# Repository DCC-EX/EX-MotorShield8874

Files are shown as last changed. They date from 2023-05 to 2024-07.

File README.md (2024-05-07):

# EX-Motorshield8874

## Overview
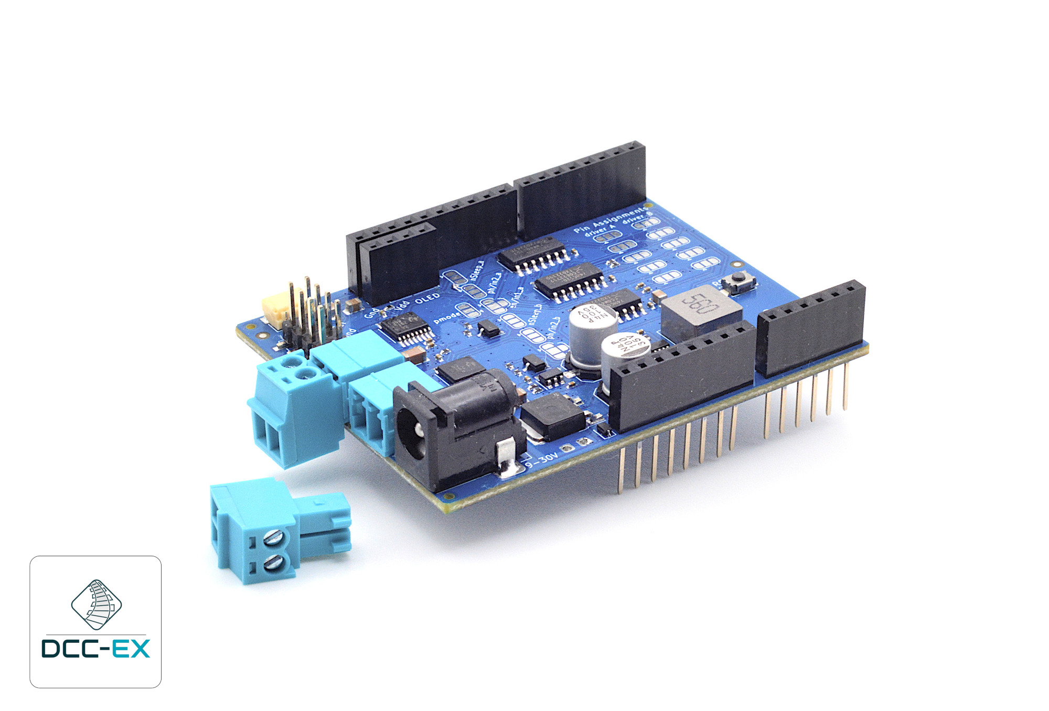
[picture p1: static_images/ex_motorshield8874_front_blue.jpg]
DCC-EX EX-MotorShield8874


The EX-Motorshield8874 is a pin compatible with the original [Arduino Motor Shield Rev3](https://store.arduino.cc/products/arduino-motor-shield-rev3) but provides significantly improved electrical performance for driving higher loads, with lower power dissipation, and improved usability.

The EX-Motorshield8874 is based on two DRV8874 H-bridge motor drivers with integrated current sensing from Texas Instruments (TI). It is used to drive inductive loads like relays, solenoids, DC and stepping motors.

Powering of Arduino motherboard is possible due to the onboard DC/DC buck converter, supporting a wide input supply range from 9 to 30V. The reverse polarity protection prevents damage to the circuit and its components in case the power supply is accidentally connected with reversed polarity.

This Shield features a green status LED which provides a visual indication of the power supply status.

### Compatibility with [Arduino Motor Shield Rev3](https://store.arduino.cc/products/arduino-motor-shield-rev3)

The EX-MotorShield8874 is pin compatible with the original Arduino Motor Shield but provides significantly improved electrical performance for driving higher loads. Input voltage range is 9-30VDC and the maximum peak output is 5A per channel, in contrast to 5-12VDC and 2A peak for the original Arduino Motor Shield.

There is also almost no voltage drop incurred from the input voltage due to the MOSFET based design, unlike the bipolar L298 used in the Arduino Motor Shield. For DCC and DC PWM model railway use, a range of 10-24VDC is recommended depending on scale.

### Motor Driver Configuration for DCC-EX EX-CommandStation

The EX-MotorShield8874 will work with the `STANDARD_MOTOR_SHIELD` definitions in `MotorDrivers.h`, but that is not ideal for several reasons. It will both unnecessarily limit current output, ignore the fault pin, and not read current correctly.

The following motor definitions are required, and appear in later versions of EX-CommandStation, with the tag `EX8874_SHIELD`, which will differ according to whether the Command Station is an UNO or Mega with 5V 10-bit ADC, or a 3.3V capable system with 12-bit ADC:

```c++
// EX 8874 based shield connected to a 5V system (like Arduino UNO/Mega) and 10bit (1024) ADC
#define EX8874_SHIELD F("EX8874"), \
 new MotorDriver( 3, 12, UNUSED_PIN, 9, A0, 5.08, 5000, A4), \
 new MotorDriver(11, 13, UNUSED_PIN, 8, A1, 5.08, 5000, A5)

// EX 8874 based shield connected to a 3V3 system with 12-bit (4096) ADC
#define EX8874_SHIELD F("EX8874"), \
 new MotorDriver( 3, 12, UNUSED_PIN, 9, A0, 1.27, 5000, A4), \
 new MotorDriver(11, 13, UNUSED_PIN, 8, A1, 1.27, 5000, A5)
```

## Control Pin Assignments

### Default Pin Assignment for DCC-EX/Arduino motor control

The EX-MotorShield8874 has the following default pin assignment for control pins on the Arduino header, and is used for full Arduino Motor Shield R3 compatibility when used for DCC-EX EX-CommandStation.

| Function | Channel A Pin | Channel B Pin |
|---|---|---|
| PWM       | D3  | D11 |
| Direction | D12 | D13 |
| Brake     | D9  | D8 |
| Current sensing | A0 | A1 |
| Fault_N   | A4  | A5 |

Default pin assignment is used for DCC-EX command stations, and has the DRV8874 mode select pin `PMODE` = high.

### Alternative Pin Assignment for DCC-EX/Arduino motor control 

All motor control signals can be connected to two different Adruino header pins. Selecting between the default pin out and the alternative pin out is done via solder jumpers on the PCB which must be first cut to disable the default position, then solder applied to select the alternate position.

| Function | Channel A Pin | Channel B Pin |
|---|---|---|
| PWM       | D2  | D5 |
| Direction | D10 | D4 |
| Brake     | D7  | D6 |
| Current sensing | A2 | A3 |
| Fault_N   | D0  | D1 |

NB: For DCC-EX control, these are not ideal pin assignments and are intended for future support of stacking of two shields. Further documentation updates will be available once testing of this mode is complete.

### Fault indicator

The H-Bridges are protected against supply undervoltage, charge pump undervoltage, output overcurrent and device overtemperature. Fault conditions are indicated on the pin `nFAULT` of the H-Bridge driver. The open drain output of the fault indicator is pulled low during a fault condition and pulled to high with the on board pull-up resistor. There is one fault indicator per channel.

**NOTE for UNO users:** the `nFAULT` pins are routed to the same pins used for I2C on the ATMEGA329P used on the Arduino UNO R3, namely A4 and A5. As such, if you are to use an EX-MotorShield8874 on an Arduino UNO, please cut the default track on the relevant jumpers to disable them. If you want to use the `nFault` pins you will need to manually jumper them to any available alternate digital input pins, then configure the Motor Driver entry in EX-CommandStation to suit the pins used.

### Alternative pin assignment for other motor control applications

The alternative pin assignment for motor control (PH/EN mode) allows to control the motor in a speed and direction type interface. This mode is selected via Jumper J101 (DRV8874 mode select pin `PMODE` = low) and is NOT required for use with DCC-EX. It is documented for completeness.

| Function | Channel A Pin | Channel B Pin |
|---|---|---|
| PH       | D3  | D11 |
| EN | D12 | D13 |
| Brake     | D9  | D8 |
| Current sensing | A0 | A1 |
| Fault_N   | A4  | A5 |

## Electrical Parameters

The DCC-EX Motor Shield provides the following electrical parameters.

| Parameter | Value |
|---|---|
| Operating voltage range | 9-30VDC, polarity protected|
| Maximum H-bridge current  | 5A peak per channel |
| Arduino supply voltage output (VIN) | 7.2V@2A max |
| IO voltage              | 3.3 and 5V, using IOREF by default |
| I2C connectivity        | Dupont, 2.54mm dual row pin, and STEMMA QT/Qwiic Headers |
| Current sensing         | Yes, adjusts range to IOREF voltage |
| Control modes possible | PWM, by default, PH/EN via jumper |

## Current Sensing

Current sensing is independently available for each channel. The Arduino IOREF supply voltage is sensed automatically, and adjusts the gain factor for the current sensing to take advantage of the full ADC input voltage range for 5V or 3.3V microcontrollers. The sense factors are calculated as follows for DCC-EX motor driver definitions:

| IOREF Voltage: | 5V | 3V3 |
|---|----|-----|
| 10-bit ADC, 1024 count | 5.08 | 4.94 |
| 12-bit ADC, 4096 count | 1.27 | 1.24 |

These values have been incorporated into EX-CommandStation Motor Driver definitions, so selecting `EX8874_SHIELD` as the `MOTOR_SHIELD_TYPE` in config.h will configure it correctly.

## Track LEDs

LEDs are provided for each channel, indicating the corresponding H-Bridge is supplying power to output connectors.

## Header Pin Assignments

The following pin assignments have been used for the various connectors.

### I2C Headers

Three I2C expansion headers (Dupont, dual-row 8-pin, and STEMMA QT/Qwiic) allow connecting either an OLED display or other additional I2C based devices.

#### Arduino Header

On the Arduino header, the default upper right I2C pins are used for I2C:

| Function | UNO R3 Pin | Mega Pin |
|---|---|---|
| SCL | D18/A5 | D21 |
| SDA | D19/A4 | D20 |

#### DIP Header

The dual-row 8-pin header has the following pin assignments:

| Function | Odd Pin | Even Pin |
|---|---|---|
| IOREF | 1 | 2 |
| SDA | 3 | 4 |
| GND | 5 | 6 |
| SCL | 7 | 8 |

#### OLED Header

The single-row 4-pin OLED header has the following pin assignments, which are standard for many I2C capable OLED displays:

| Function | Pin |
|---|---|
| GND | 1 |
| IOREF | 2 |
| SCL | 3 |
| SDA | 4 |

#### STEMMA QT/Qwiic Connector

STEMMA QT/Qwiic connector pin assignments are per the standard, but included for completeness:

| Function | Pin | Colour Code |
|---|---|---|
| GND | 1 | Black |
| 3v3 | 2 | Red |
| SDA | 3 | Blue |
| SCL | 4 | Yellow |

**NOTE** STEMMA QT power is tied to 3v3 as that is required for the standard. When using the EX-MotorShield8874 with 5V motherboards such as UNO and Mega, any I2C peripherals connected to the STEMMA QT connector **must** be 5V-tolerant only!

Pull-up resistors for the I2C communication are not populated by default. If required, pull-up resistors (R101, R102) can be populated on the board, though this is typically not necessary.

## Reset button

A reset button is provided to reset the Arduino board.

## PCB Jumpers

Various PCB jumpers are provided to alter functionality of the board to suit user needs. These include jumpers to alter pin assignments for driving the motor shield, to disable the onboard 7.2V regulator or disconnect it from the VIN, and jumpers to override the IOREF pin for ADC range selection.

### Aternate Pin Assignment PCB Jumpers

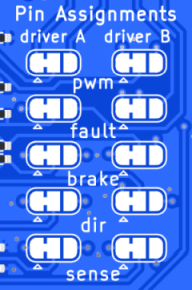
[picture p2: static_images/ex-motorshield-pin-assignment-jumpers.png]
Alternate_Pin_Assignments


There are 5 sets of PCB jumpers for each motor driver IC, some or all of which can be used to reassign Arduino pins to the various logic functions. The table below lists them in order as they appear on the PCB:

| Function | Driver A Default | Driver A Alternate| Driver B Default | Driver B Alternate |
|---|---|---|---|---|
| PWM       | D3  | D2 | D11 | D5 |
| Fault | A4  | D0 | A5 | D1 |
| Brake | D9  | D7 | D8 | D6 |
| Direction | D12 | D10 | D13 | D4 |
| Current sense | A0 | A2 | A1 | A3 |

### Power Configuration PCB Jumpers

There are 4 sets of PCB jumpers to change the way power is handled on the board. One on the top of the board, and 3 on the bottom, shown here:

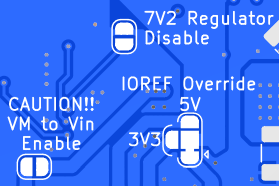
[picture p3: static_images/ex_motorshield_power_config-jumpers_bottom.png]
Bottom_Power_Config_Jumpers
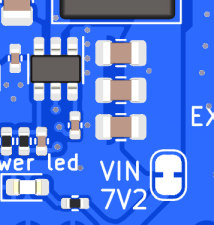
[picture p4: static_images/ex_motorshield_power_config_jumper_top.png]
Top_Power_Config_Jumper
 

| Jumper | Function |
|---|---|
| Regulator Disable (Regulator Enable on Rev A boards) | Defaults to *ENABLED*. Rev B boards, *solder* between pads to DISABLE onboard 7.2V regulator. Rev A boards *cut* between pads to DISABLE |
| IOREF Override | Defaults to IOREF used as power source, cut and then solder to either 5V or 3V3 to power logic and current sense |
| VM to Vin Enable (unlabelled on Rev A boards) | Defaults to NOT connected. CAUTION: soldering these pads CONNECTS motor power to VIN and should not be needed |
| VIN | Defaults to ON, cut to stop providing regulated 7.2V power to VIN to power the Arduino |

## Manufacturing Notes

### Bill of Materials (BOM)

The bill of materials spreadsheet above is optimised for manufacture at JLCPCB (https://jlcpcb.com/) at present, and will allow assembly of all components except the DC barrel jack, motor output connectors and Arduino shield stackable headers.

### PCB Material Specifications

For best performance, 1oz copper for both outer and inner layers of this 4-layer PCB are safest. Of course 2oz copper can be specified, but this is not deemed necessary from testing so far and cost may be prohibitive. Also, using FR-4 TG155 will give additional safety margin. The design can be made lead-free, provided all components are also lead-free types. JLCPCB currently does not have lead-free connectors for DCC track or DC input power, so those components are not in the default Bill of Materials (BOM).

## Stacking Multiple Shields

It is possibile to stack two EX-MotorShield8874s, and even stack an EX-MotorShield and a Arduino Motor Shield.

Produktfoto_3_4

There are two different proposed operating modes possible:

1. **Independent district mode:** The DCC-EX Motor Shields are controlled independently using different control signals. This allows a total 4 independent H-Bridges to be driven completely independently for separate DCC or DC PWM districts.
2. **Parallel booster mode:** Both EX-MotorShield8874s are controlled with the same control signals so both pairs of H-bridges are running in parallel. This mode is used to increase the current capabilities of the 2 DCC or DC PWM districts.

***CAUTIONARY NOTE:*** Only one EX-MotorShield8874 should provide power to the underlying motherboard from the DCC power feed! The jumper connecting the top VIN feed pin from the onboard 7.2V regulator to the Arduino sheild connectors must be cut on one of the stacked shields. It is also advisable to cut the ENABLE pin for the onboard regulator as that will turn it off completely as well. (See documentation of Power Configuration PCB Jumpers, above!)

This information is provided for reference. For full documentation, please visit this section on our website; [Stacking EX-MotorShields](https://dcc-ex.com/reference/hardware/motorboards/ex-motor-shield-8874.html#stacking-ex-motorshield8874s)

## Version History

**Rev B2**
* Changed the AOD4185 reverse voltage protection mosfet (Q201) in a TO-252-2 package to an AO4407C in an SOIC-8 package to save board space.

**Rev B**
* Changed 7.2V Regulator from MP9942GJ-Z to TPS54302 due to availability issues. NOTICE: This forced the Regulator Enable/Disable to be reversed from the Rev A board. The Rev A board jumper pad must be *cut* to disable the regulator and is named "Regulator Enable". On the Rev B board, the jumper must be *solder bridged* to to disable the regulator and is labelled "7V Regulator Disable".
* The regulator change necessitated changing Inductor L201 from 56uH to 15uH.

**Rev A2**
* Added 47k pulldown resistors (R103 and R104) to the enable pins to prevent possible DCC or DC voltage pulses to the outputs until the command station is able to set the GPIO pins to a stable state during boot up.
* Added more descriptive silkscreen labelling.
* Removed solder mask from jumper pads to make it easier to see which are bridged and which are open.

**Rev A**
* First version of the EX-MotorShield8874. NOTICE: It may be necessary to add 47k pulldown resistors between pwm_a and pwm_b and GND. These are the "enable" pins that turn power on to the track outputs. With the pins floating, it is possible that brief DC power can be applied to the track until the command station fully boots. If configured for the STANDARD_MOTOR_SHIELD, this is as simple as inserting one end of a resistor into pin 3 of the header and the other end to a GND header pin, and the other resister between pin 11 and GND. If using a different motor driver definition, use the enable pins for that definition.

## Reference

- [Schematic](./static_images/EX-MotorShield8874Schematic_RevB2.pdf)
- [DRV8874 Datasheet](https://www.ti.com/product/DRV8874?keyMatch=DRV8874&tisearch=search-everything&usecase=GPN)

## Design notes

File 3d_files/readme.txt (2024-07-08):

Folder to hold 3d models in step file format for use under license for the EX-MotorShield8874

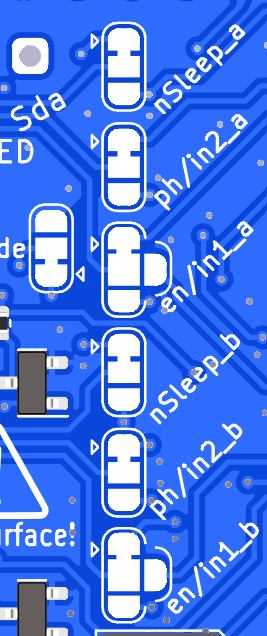
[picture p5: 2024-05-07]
static_images/ex_motorshield_jumper_pads.png

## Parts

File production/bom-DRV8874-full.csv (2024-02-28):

Designator | Footprint | Quantity | Value | LCSC Part #
C101, C104, C107, C108, C114, C115, C208, C220, C221, C222 | C_1005_(0402) | 10 | 100n | C1525
C102, C105, C203, C209, C210 | 1206 | 5 | 10u VM | C13585
C103, C106, C211 | C_1005_(0402) | 3 | 100n VM | C307331
C109, C110 | C_1005_(0402) | 2 | 22n VM | C337699
C111, C212, C213, C214, C216, C217, C218, C219 | 805 | 8 | 22u | C45783
C112, C113 | C_1005_(0402) | 2 | 22n | C337699
C201, C202 | CP_Elec_6.3x7.7 | 2 | 100u VM | C2972719
C215 | C_1005_(0402) | 1 | 56p | C107007
D101, D102, D103, D104 | 603 | 4 | 0603_LED_Yellow | C72038
D201 | D_SOD-323 | 1 | 10V | C85383
D202 | 603 | 1 | 0603_LED_Green | C72043
J101, J103 | PhoenixContact_MC_1,5_2-G-3.5_1x02_P3.50mm_Horizontal_edited | 2 | MC 1,5/ 2-G-3,5 | C409115
J105 | JST_SH_SM04B-SRSS-TB_1x04-1MP_P1.00mm_Horizontal | 1 | STEMMA QT | C160404
J106 | PinHeader_2x04_P2.54mm_Vertical_SMD | 1 | Conn_02x04_smd | C780053
J107 | PinHeader_1x04_P2.54mm_Vertical_solderpad | 1 | Conn_01x04_f | C2685089
J201 | BarrelJack_2.1mm_SMD | 1 | Barrel_Jack_MountingPin | C319134
L201 | L_7.1x6.6_H3_SLO0630H | 1 | 15uH | C182182
Q101, Q102 | SOT-23 | 2 | AO3400A | C20917
Q201 | SOIC-8_3.9x4.9mm_P1.27mm | 1 | AO4407C | C469397
R101, R102, R103, R104, R107, R108, R109, R110, R201, R202 | R_1005_(0402) | 10 | 47k | C163440
R111, R112 | R_1005_(0402) | 2 | 1k43 | C226851
R113, R114 | R_1005_(0402) | 2 | 732R | C321605
R115, R204 | R_1005_(0402) | 2 | 9k1 | C25926
R116, R203 | R_1005_(0402) | 2 | 100k | C60491
SW101 | SW_SPST_TS-1088-AR02016 | 1 | Switch | C720477
U101 | SO-14_3.9x8.65mm_P1.27mm | 1 | 74HC04 | C5590
U102 | SO-14_3.9x8.65mm_P1.27mm | 1 | 74HC08 | C5593
U103 | SO-14_3.9x8.65mm_P1.27mm | 1 | 74HC32 | C5632
U104, U105 | HTSSOP-16-1EP_4.4x5mm_P0.65mm_EP3.4x5mm_Mask2.46_HiAmp | 2 | DRV8874PWPR | C1855818
U106 | SOT-23-5 | 1 | LMV321 | C7972
U201 | SOT-23-6 | 1 | TPS54302 | C311983

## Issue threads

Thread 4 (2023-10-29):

Inrush current triggers fault

higaski, 2023-10-29:
Hello

Out of curiosity, have you ever fixed the issue described in the e2e forum here: https://e2e.ti.com/support/motor-drivers-group/motor-drivers/f/motor-drivers-forum/1249338/drv8874-unrush-current-trippling-fault-due-to-capacitance-of-circuit

There is an accepted answer (green border around a post?) which mentions to put the IMODE pin into STATE Quad-Level 2 (basically adding 20k to GND), but from how I understand the datasheet that wouldn't really fix things and an overcurrent fault would still occur.

I'm thinking about putting a 1uH // 2R filter on the output stage to solve this.

pmantoine, 2024-02-27:
We have not tried the 1uH/2R filter... we instead switch briefly to high frequency PWM mode in software to handle in-rush, then switch back to DCC mode. This appears to work. Have you tried the 1uH/2R solution?

higaski, 2024-02-27:
No, I'm no longer using this device.

crosland, 2024-07-06:
> we instead switch briefly to high frequency PWM mode in software to handle in-rush, then switch back to DCC mode. This appears to work.

Does this mean the output is not DCC during startup?

pmantoine, 2024-07-07:
> > we instead switch briefly to high frequency PWM mode in software to handle in-rush, then switch back to DCC mode. This appears to work.
>
> Does this mean the output is not DCC during startup?

Only if a short is detected at switch on, and only very briefly, sufficient to charge capacitors causing the in-rush issue in the first place.

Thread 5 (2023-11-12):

Schematics PDF missing the DC-DC page

chatelao, 2023-11-12:
:-)

chatelao, 2023-11-13:
Sorry, this was a mobile viewer issue only.

Closed 2023-11-13.

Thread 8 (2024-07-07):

Output Current Specifications

crosland, 2024-07-07:
What is the maximum long term sustained output current spec per channel?

What copper weight is used for the PCB?

According to the DRV8874 thermal data, the peak of 5A will not be maintained for very long.

crosland, 2024-09-12:
Anyone?

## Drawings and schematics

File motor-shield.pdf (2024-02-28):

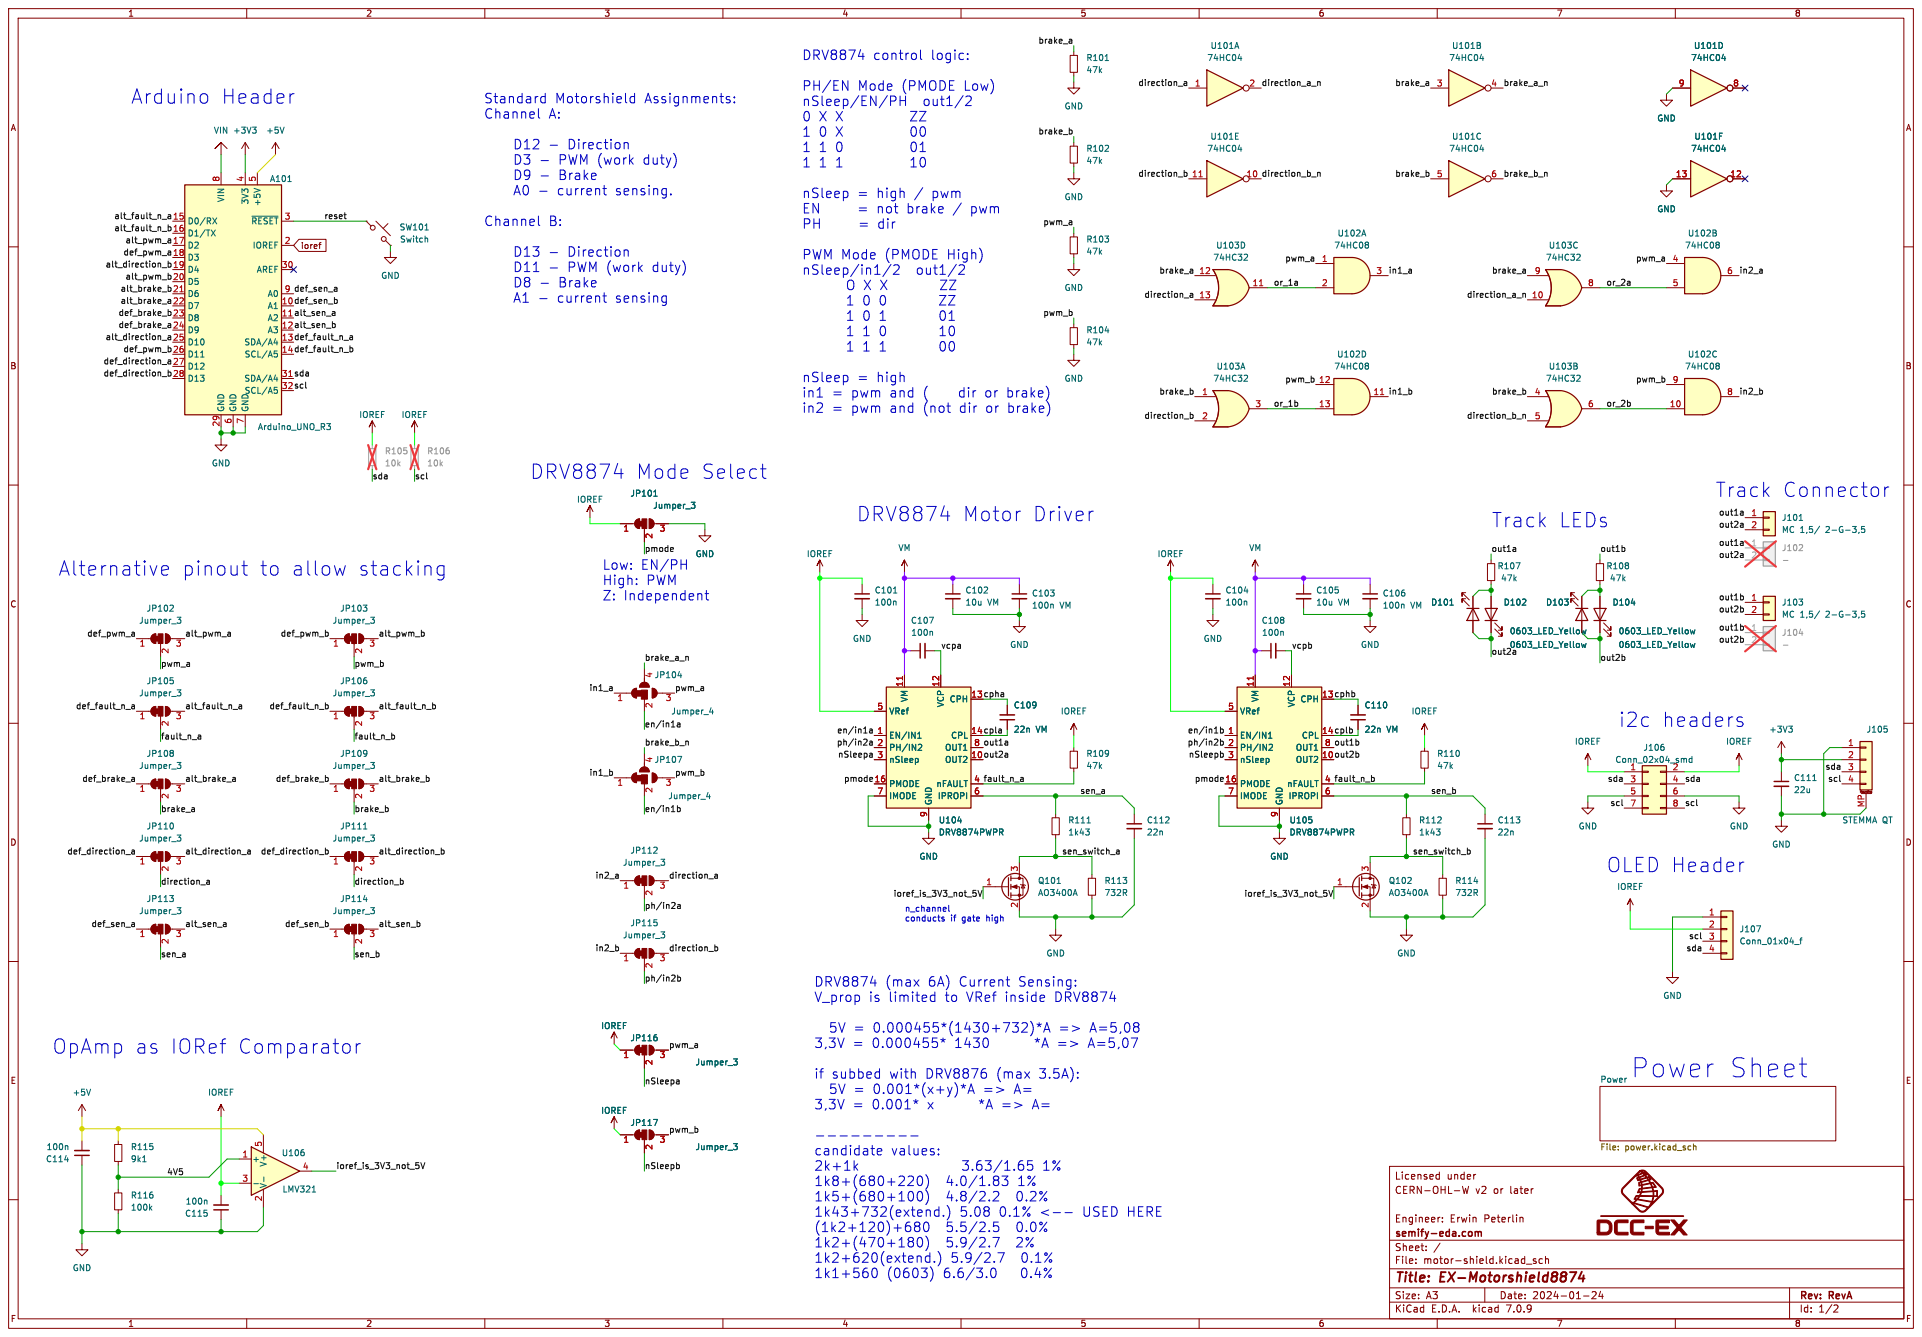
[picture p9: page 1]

PH/EN Mode (PMODE Low)

~{RESET}3 AREF 30 SDA/A4 31 SCL/A5 32 3V3

A1 10 A2 11 A3 12 SDA/A4 13 SCL/A5 14 D0/RX 15 D1/TX 16 D2 17 D3 18 D4 19

PWM Mode (PMODE High)

nSleep = high
in2 = pwm and (not dir or brake)

DRV8874 (max 6A) Current Sensing:
V_prop is limited to VRef inside DRV8874

OpAmp as IORef Comparator

if subbed with DRV8876 (max 3.5A):

File: motor-shield.kicad_sch Sheet: / semify-eda.com

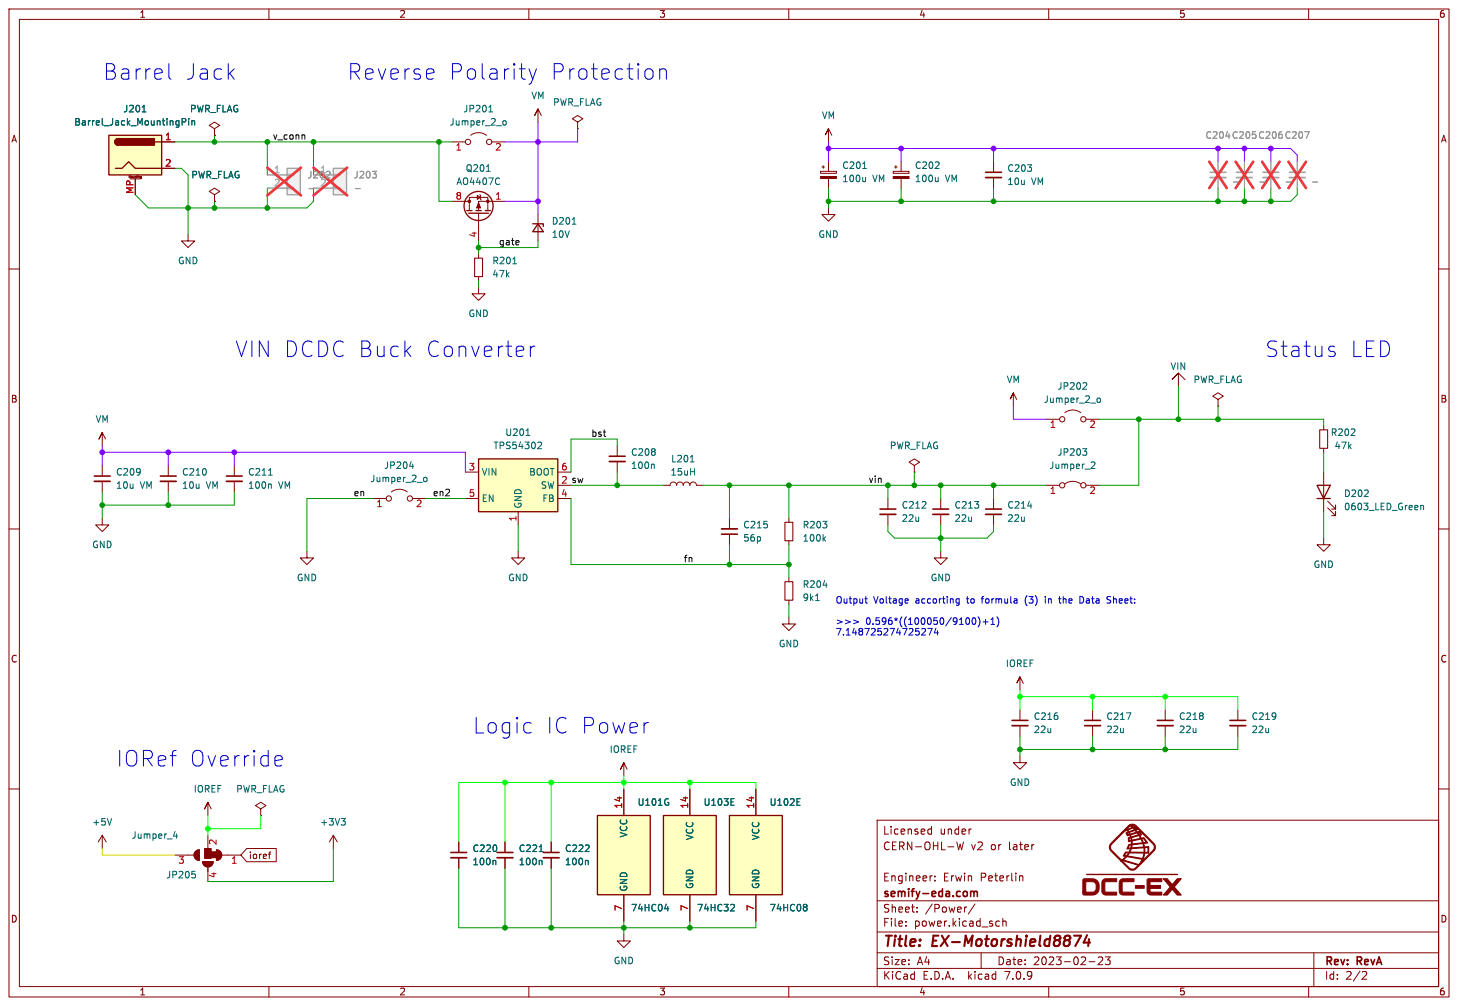
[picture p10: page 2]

sw VIN DCDC Buck Converter

1 SW 2 VIN 3 FB 4 EN 5 BOOT 6 U201 TPS54302 C219

File: power.kicad_sch Sheet: /Power/ semify-eda.com

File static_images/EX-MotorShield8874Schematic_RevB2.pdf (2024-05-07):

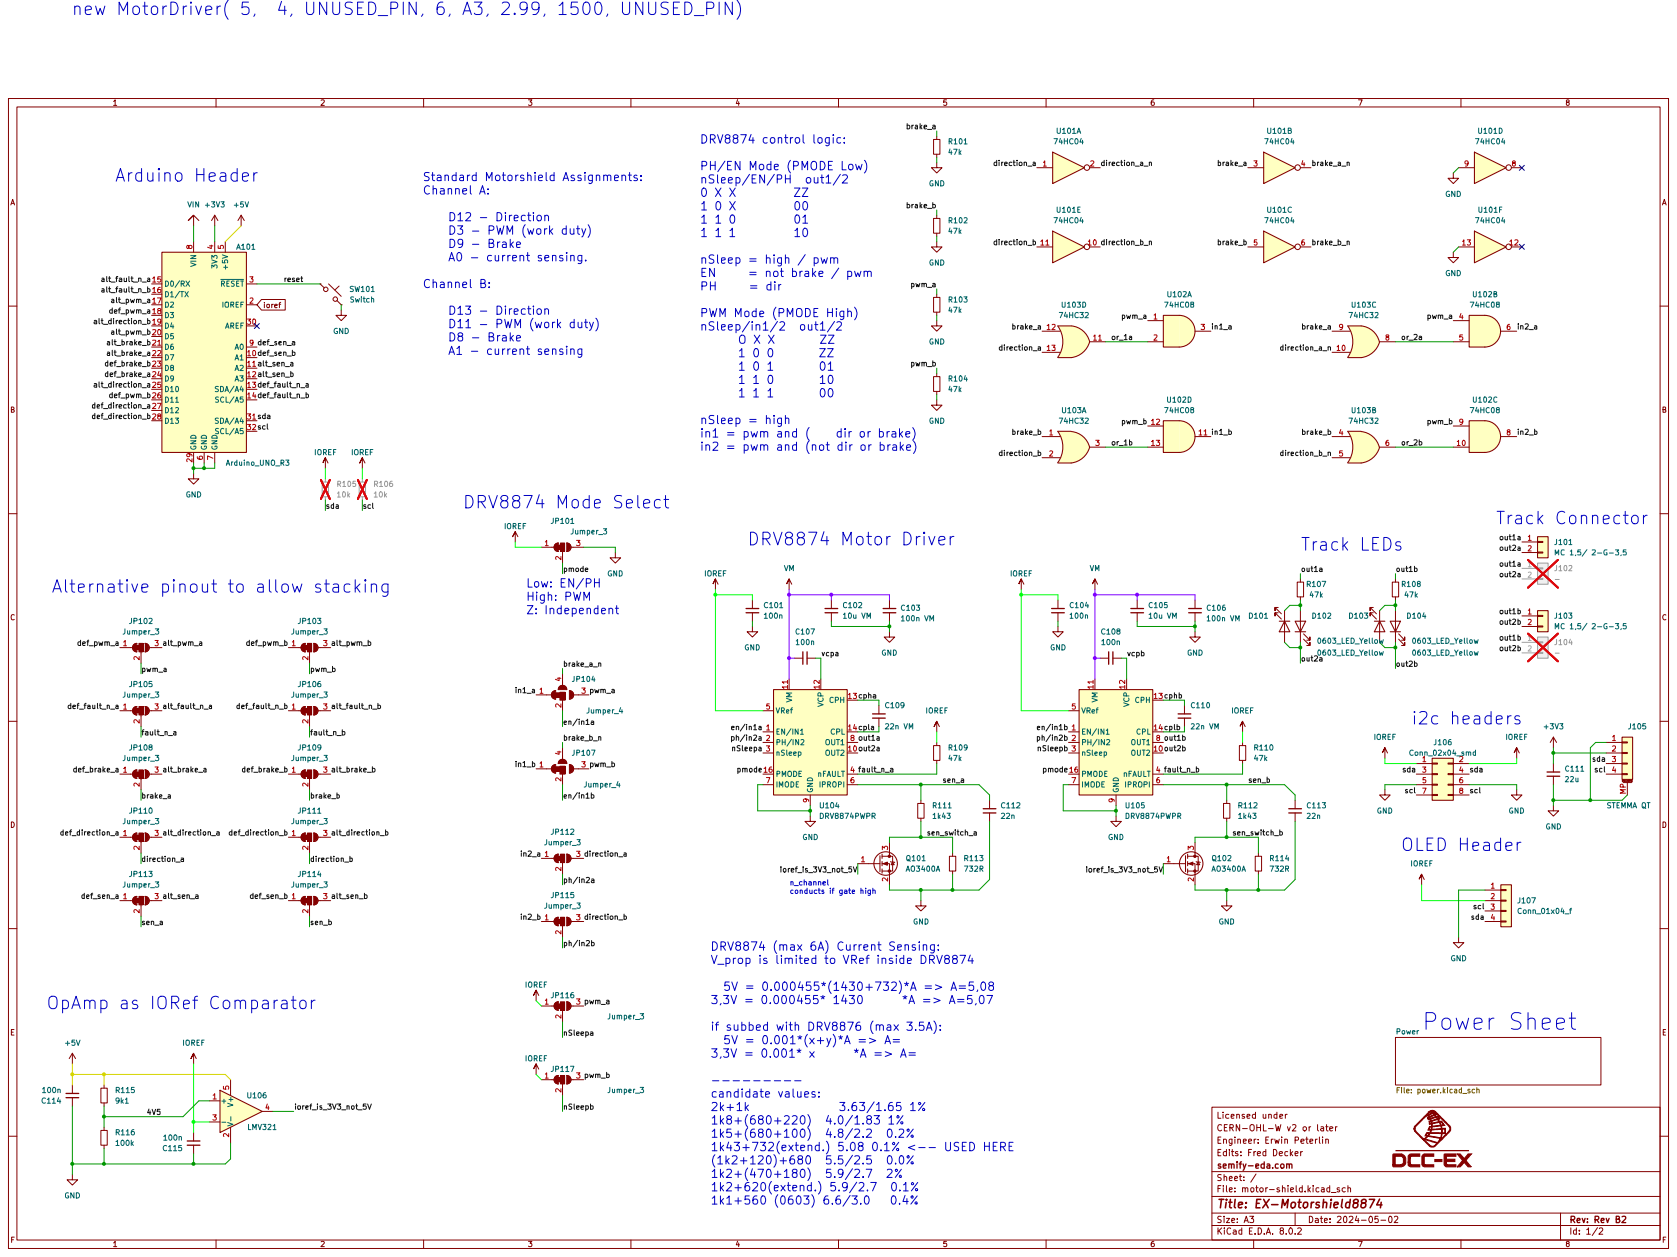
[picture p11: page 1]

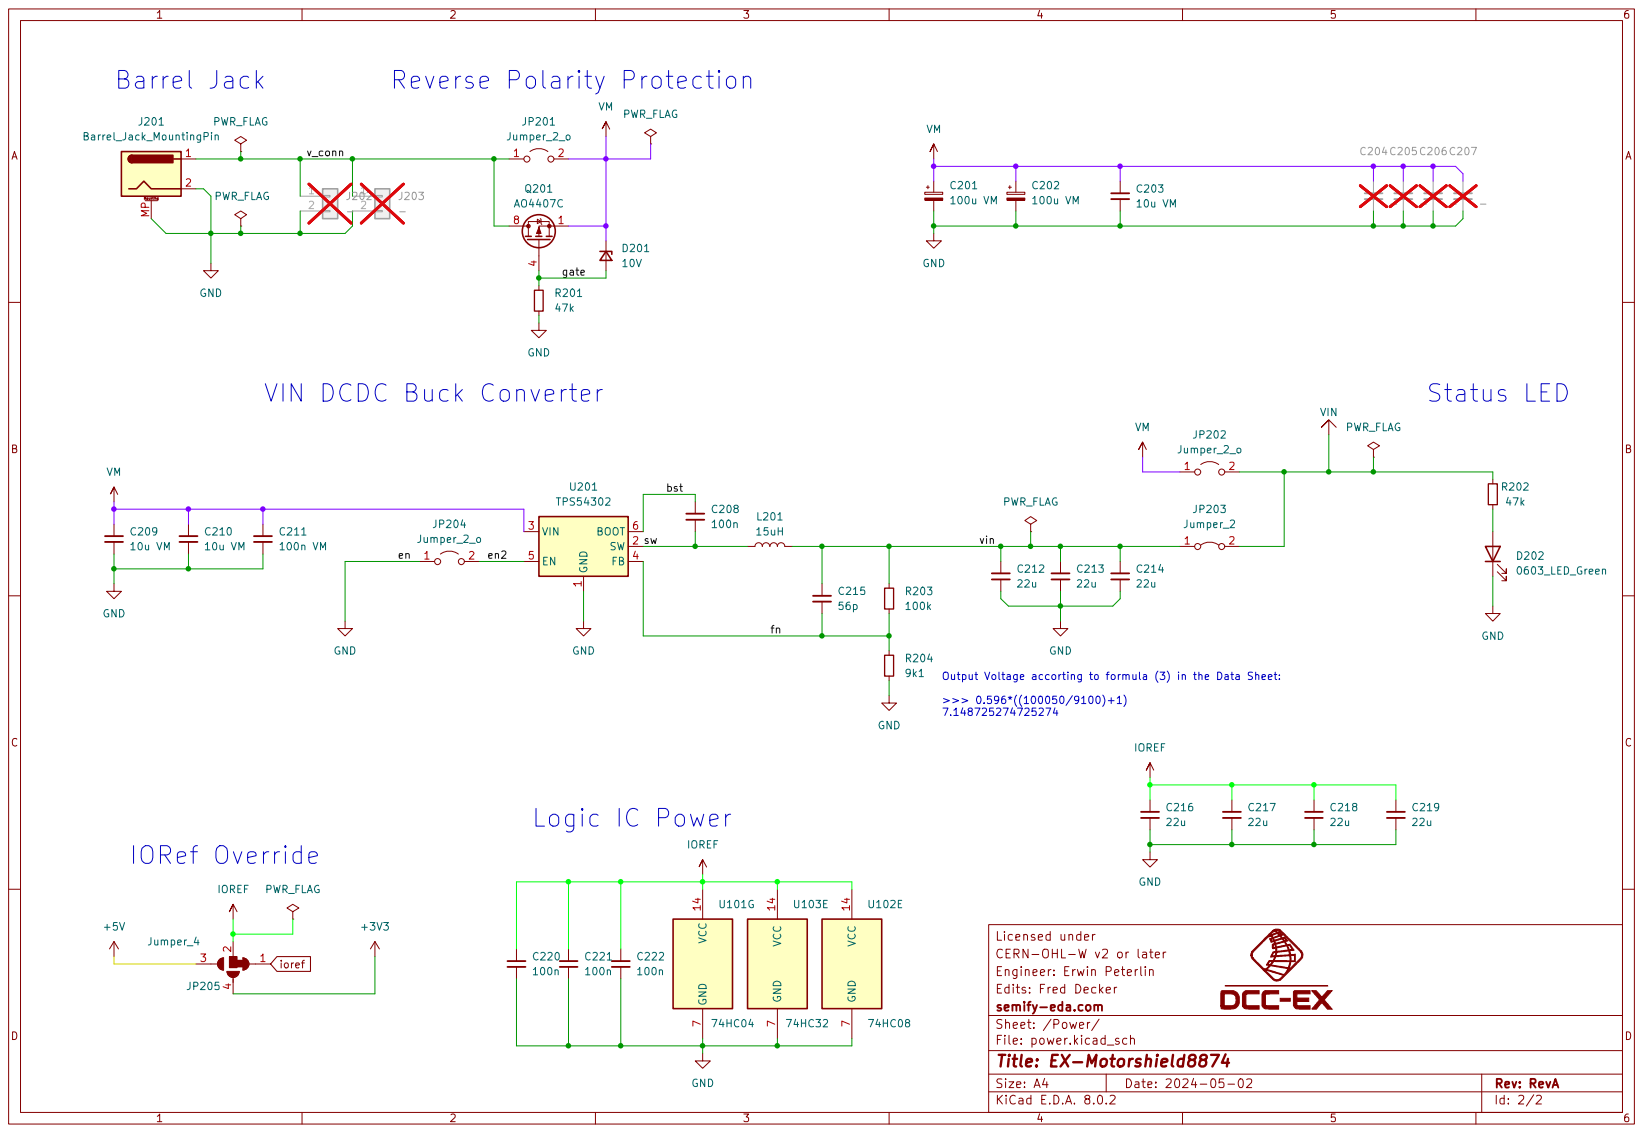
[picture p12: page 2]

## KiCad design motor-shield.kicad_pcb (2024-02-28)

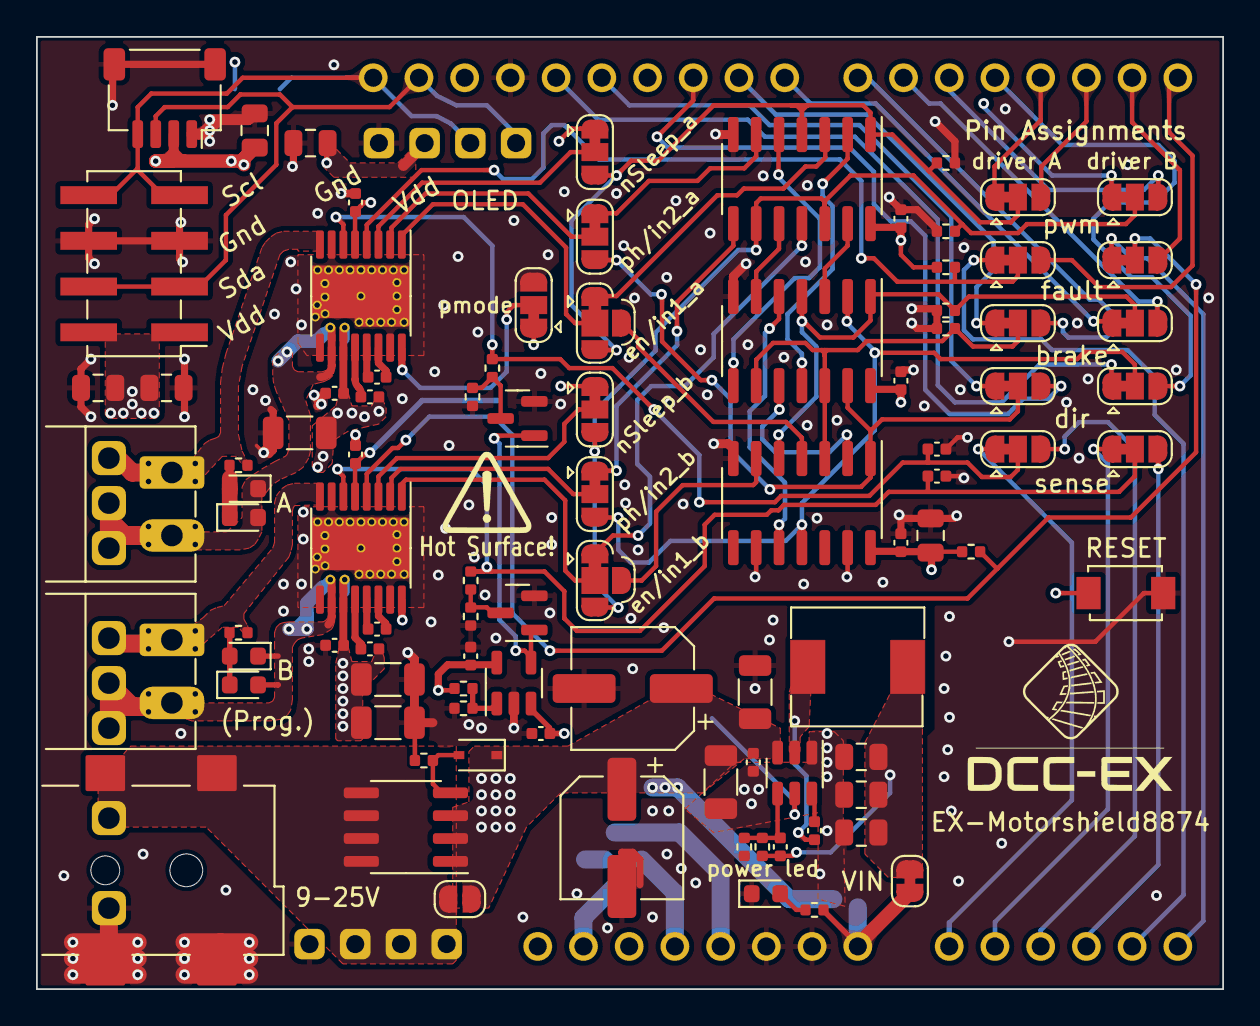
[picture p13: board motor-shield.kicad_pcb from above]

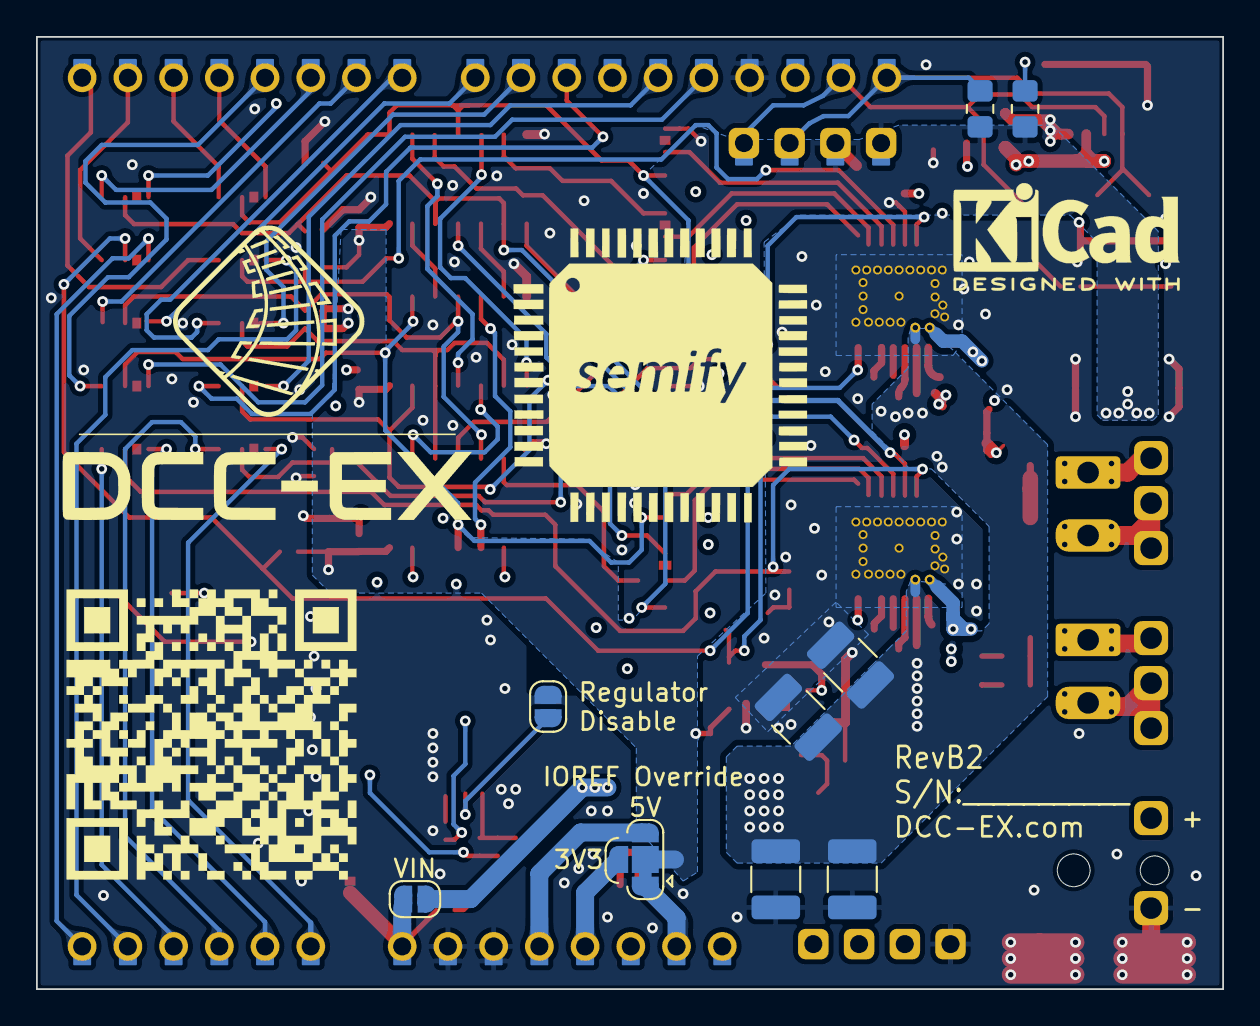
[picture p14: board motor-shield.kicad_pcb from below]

Board: 4 copper layers, 65.9 x 52.9 mm, 108 parts (10 on the bottom side), 83 nets.

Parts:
A101: Arduino_UNO_R3; Arduino_UNO_R3_edit
C101, C104, C107, C108, C114, C115, C208, C220, C221, C222: 100n; C_1005_(0402)
C102, C105, C203, C209, C210: 10u VM; C_1206_3216Metric
C103, C106, C211: 100n VM; C_1005_(0402)
C109, C110: 22n VM; C_1005_(0402)
C111, C212, C213, C214, C216, C217, C218, C219: 22u; C_0805_2012Metric
C112, C113: 22n; C_1005_(0402)
C201, C202: 100u VM; CP_Elec_6.3x7.7
C204, C205, C206, C207: -; C_1210_3225Metric_Pad1.33x2.70mm_HandSolder
C215: 56p; C_1005_(0402)
D101, D102, D103, D104: 0603_LED_Yellow; LED_0603_1608Metric
D201: 10V; D_SOD-323
D202: 0603_LED_Green; LED_0603_1608Metric
J101, J103: MC 1,5/ 2-G-3,5; PhoenixContact_MC_1,5_2-G-3.5_1x02_P3.50mm_Horizontal_edited
J102, J104: -; PinHeader_01x03_P2.5mm_Vertical_min
J105: STEMMA QT; JST_SH_SM04B-SRSS-TB_1x04-1MP_P1.00mm_Horizontal
J106: Conn_02x04_smd; PinHeader_2x04_P2.54mm_Vertical_SMD
J107: Conn_01x04_f; PinHeader_1x04_P2.54mm_Vertical_solderpad
J201: Barrel_Jack_MountingPin; BarrelJack_2.1mm_SMD
J202: -; PinHeader_01x02_P5mm_Vertical_min
J203: -; PinHeader_1x04_P2.54mm_Vertical_min_1
JP101, JP102, JP103, JP105, JP106, JP108, JP109, JP110, JP111, JP112, JP113, JP114, JP115, JP116, JP117: Jumper_3; SolderJumper-3
JP104, JP107, JP205: Jumper_4; SolderJumper-4
JP201, JP202, JP204: Jumper_2_o; SolderJumper-2_P1.3mm_Open_RoundedPad1.0x1.5mm
JP203: Jumper_2; SolderJumper-2_P1.3mm_Bridged
L201: 15uH; L_7.1x6.6_H3_SLO0630H
Q101, Q102: AO3400A; SOT-23
Q201: AO4407C; SOIC-8_3.9x4.9mm_P1.27mm
R101, R102, R103, R104, R107, R108, R109, R110, R201, R202: 47k; R_1005_(0402)
R105, R106: 10k; R_0805_2012Metric_Pad1.20x1.40mm_HandSolder
R111, R112: 1k43; R_1005_(0402)
R113, R114: 732R; R_1005_(0402)
R115, R204: 9k1; R_1005_(0402)
R116, R203: 100k; R_1005_(0402)
SW101: Switch; SW_SPST_TS-1088-AR02016
U101: 74HC04; SO-14_3.9x8.65mm_P1.27mm
U102: 74HC08; SO-14_3.9x8.65mm_P1.27mm
U103: 74HC32; SO-14_3.9x8.65mm_P1.27mm
U104, U105: DRV8874PWPR; HTSSOP-16-1EP_4.4x5mm_P0.65mm_EP3.4x5mm_Mask2.46_HiAmp
U106: LMV321; SOT-23-5
U201: TPS54302; SOT-23-6

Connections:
+3V3: A101.4 (3V3), C111.1, J105.2, JP205.4 (D)
+5V: A101.5 (+5V), C114.2, JP205.3 (B), R115.1, U106.5 (V+)
/4V5: R115.2, R116.1, U106.1 (+)
/Power/bst: C208.1, U201.6 (BOOT)
/Power/en2: JP204.2 (B), U201.5 (EN)
/Power/fn: C215.1, R203.2, R204.1, U201.4 (FB)
/Power/gate: D201.2 (A), Q201.4 (G), R201.1
/Power/sw: C208.2, L201.1, U201.2 (SW)
/Power/v_conn: J201.1, J202.1, J203.1, JP201.1 (A), Q201.5 (D), Q201.6 (D), Q201.7 (D), Q201.8 (D)
/Power/vin: C212.1, C213.1, C214.1, C215.2, JP203.1 (A), L201.2, R203.1
/alt_brake_a: A101.22 (D7), JP108.3 (B)
/alt_brake_b: A101.21 (D6), JP109.3 (B)
/alt_direction_a: A101.25 (D10), JP110.3 (B)
/alt_direction_b: A101.19 (D4), JP111.3 (B)
/alt_fault_n_a: A101.15 (D0/RX), JP105.3 (B)
/alt_fault_n_b: A101.16 (D1/TX), JP106.3 (B)
/alt_pwm_a: A101.17 (D2), JP102.3 (B)
/alt_pwm_b: A101.20 (D5), JP103.3 (B)
/alt_sen_a: A101.11 (A2), JP113.3 (B)
/alt_sen_b: A101.12 (A3), JP114.3 (B)
/brake_a: JP108.2 (C), R101.1, U101.3, U103.9, U103.12
/brake_a_n: JP104.4 (D), U101.4
/brake_b: JP109.2 (C), R102.1, U101.5, U103.1, U103.4
/brake_b_n: JP107.4 (D), U101.6
/cpha: C109.2, U104.13 (CPH)
/cphb: C110.2, U105.13 (CPH)
/cpla: C109.1, U104.14 (CPL)
/cplb: C110.1, U105.14 (CPL)
/def_brake_a: A101.24 (D9), JP108.1 (A)
/def_brake_b: A101.23 (D8), JP109.1 (A)
/def_direction_a: A101.27 (D12), JP110.1 (A)
/def_direction_b: A101.28 (D13), JP111.1 (A)
/def_fault_n_a: A101.13 (SDA/A4), JP105.1 (A)
/def_fault_n_b: A101.14 (SCL/A5), JP106.1 (A)
/def_pwm_a: A101.18 (D3), JP102.1 (A)
/def_pwm_b: A101.26 (D11), JP103.1 (A)
/def_sen_a: A101.9 (A0), JP113.1 (A)
/def_sen_b: A101.10 (A1), JP114.1 (A)
/direction_a: JP110.2 (C), JP112.3 (B), U101.1, U103.13
/direction_a_n: U101.2, U103.10
/direction_b: JP111.2 (C), JP115.3 (B), U101.11, U103.2
/direction_b_n: U101.10, U103.5
/en/in1a: JP104.2 (C), U104.1 (EN/IN1)
/en/in1b: JP107.2 (C), U105.1 (EN/IN1)
/fault_n_a: JP105.2 (C), R109.2, U104.4 (nFAULT)
/fault_n_b: JP106.2 (C), R110.2, U105.4 (nFAULT)
/in1_a: JP104.1 (A), U102.3
/in1_b: JP107.1 (A), U102.11
/in2_a: JP112.1 (A), U102.6
/in2_b: JP115.1 (A), U102.8
/ioref_is_3V3_not_5V: Q101.1 (G), Q102.1 (G), U106.4
/nSleepa: JP116.2 (C), U104.3 (nSleep)
/nSleepb: JP117.2 (C), U105.3 (nSleep)
/or_1a: U102.2, U103.11
/or_1b: U102.13, U103.3
/or_2a: U102.5, U103.8
/or_2b: U102.10, U103.6
/out1a: J101.1, J102.1, R107.2, U104.8 (OUT1)
/out1b: J103.1, J104.1, R108.2, U105.8 (OUT1)
/out2a: D101.2 (A), D102.1 (K), J101.2, J102.2, U104.10 (OUT2)
/out2b: D103.2 (A), D104.1 (K), J103.2, J104.2, U105.10 (OUT2)
/ph/in2a: JP112.2 (C), U104.2 (PH/IN2)
/ph/in2b: JP115.2 (C), U105.2 (PH/IN2)
/pmode: JP101.2 (C), U104.16 (PMODE), U105.16 (PMODE)
/pwm_a: JP102.2 (C), JP104.3 (B), JP116.3 (B), R103.1, U102.1, U102.4
/pwm_b: JP103.2 (C), JP107.3 (B), JP117.3 (B), R104.1, U102.9, U102.12
/reset: A101.3 (~RESET), SW101.1
/scl: A101.32 (SCL/A5), J105.4, J106.7, J106.8, J107.3, R106.2
/sda: A101.31 (SDA/A4), J105.3, J106.3, J106.4, J107.4, R105.2
/sen_a: C112.1, JP113.2 (C), R111.1, U104.6 (IPROPI)
/sen_b: C113.1, JP114.2 (C), R112.1, U105.6 (IPROPI)
/sen_switch_a: Q101.3 (D), R111.2, R113.1
/sen_switch_b: Q102.3 (D), R112.2, R114.1
/vcpa: C107.2, U104.12 (VCP)
/vcpb: C108.2, U105.12 (VCP)
GND: A101.6 (GND), A101.7 (GND), A101.29 (GND), C101.2, C102.2, C103.2, C104.2, C105.2, C106.2, C111.2, C112.2, C113.2, C114.1, C115.1, C201.2, C202.2, C203.2, C204.2, C205.2, C206.2, C207.2, C209.2, C210.2, C211.2, C212.2, C213.2, C214.2, C216.2, C217.2, C218.2, C219.2, C220.2, C221.2, C222.2, D202.1 (K), J105.1, J105.MP (MountPin), J106.5, J106.6, J107.1, J201.2, J201.MP (MountPin), J202.2, J203.2, JP101.3 (B), JP204.1 (A), Q101.2 (S), Q102.2 (S), R101.2, R102.2, R103.2, R104.2, R113.2, R114.2, R116.2, R201.2, R204.2, SW101.2, U101.7 (GND), U101.9, U101.13, U102.7 (GND), U103.7 (GND), U104.7 (IMODE), U104.9 (GND), U104.15 (GND), U104.17 (GND), U105.7 (IMODE), U105.9 (GND), U105.15 (GND), U105.17 (GND), U106.2 (V-), U201.1 (GND)
IOREF: C101.1, C104.1, C115.2, C216.1, C217.1, C218.1, C219.1, C220.1, C221.1, C222.1, J106.1, J106.2, J107.2, JP101.1 (A), JP116.1 (A), JP117.1 (A), JP205.2 (C), R105.1, R106.1, R109.1, R110.1, U101.14 (VCC), U102.14 (VCC), U103.14 (VCC), U104.5 (VRef), U105.5 (VRef), U106.3 (-)
unnamed: D101.1 (K), D102.2 (A), R107.1
unnamed: D103.1 (K), D104.2 (A), R108.1
unnamed: D202.2 (A), R202.1
VIN: A101.8 (VIN), JP202.2 (B), JP203.2 (B), R202.2
VM: C102.1, C103.1, C105.1, C106.1, C107.1, C108.1, C201.1, C202.1, C203.1, C204.1, C205.1, C206.1, C207.1, C209.1, C210.1, C211.1, D201.1 (K), JP201.2 (B), JP202.1 (A), Q201.1 (S), Q201.2 (S), Q201.3 (S), U104.11 (VM), U105.11 (VM), U201.3 (VIN)
ioref: A101.2 (IOREF), JP205.1 (A)

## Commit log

2023-04-27 contribute motorshield
    [bom-DRV8874-full.csv, motor-shield.kicad_pcb, motor-shield.kicad_sch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]
2023-05-05 README - added I2C pins
2023-05-08 README pin assignments
2023-05-08 README power jumpers
2023-05-09 README power config
2023-05-09 README BOM notes
2023-05-15 PCB Manufacturing notes
2023-06-02 remove bom and pos files from gerbers.zip and move bom and pos files to production folder
    [bom-DRV8874-full.csv, positions-DRV8874-full.csv]
2023-06-05 Update to RevA1
    [bom-DRV8874-full.csv, motor-shield.kicad_pcb, motor-shield.kicad_sch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]
2023-07-08 Rev A2
    [bom-DRV8874-full.csv, motor-shield.kicad_pcb, motor-shield.kicad_sch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]
2024-01-24 update to RevB
    [bom-DRV8874-full.csv, motor-shield.kicad_pcb, motor-shield.kicad_sch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]
2024-05-07 Update README.md
    Fix motor driver config from negative fault pin values to positive
2024-05-07 Added Motorshield schematic link to readme

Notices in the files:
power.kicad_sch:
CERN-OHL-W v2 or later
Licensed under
